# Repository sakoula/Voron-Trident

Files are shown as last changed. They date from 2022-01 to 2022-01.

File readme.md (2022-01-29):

# Voron Trident

<!-- MarkdownTOC -->

- [Very Important Links](#very-important-links)
- [Crimping Microfits](#crimping-microfits)
- [Voron Afterburner PCB setup](#voron-afterburner-pcb-setup)
- [Fysetc Spider Wiring](#fysetc-spider-wiring)
- [Klipper Firmware](#klipper-firmware)
    - [Current Config](#current-config)
    - [Other Configs](#other-configs)
    - [Motor Configuration](#motor-configuration)
    - [Bed Heater Thermistor](#bed-heater-thermistor)
    - [Hotend Thermistor](#hotend-thermistor)
- [Initial Setup](#initial-setup)
    - [Motor Setup](#motor-setup)
    - [Configuring Limits](#configuring-limits)
    - [Inductive Probe](#inductive-probe)
    - [PID Tune](#pid-tune)
    - [Bed Levelling](#bed-levelling)
    - [Z Offset Adjustment](#z-offset-adjustment)
    - [FUN](#fun)
    - [Extruder Calibration \(e-steps\)](#extruder-calibration-e-steps)
    - [Bed Mesh](#bed-mesh)
- [Notes from Steve Build](#notes-from-steve-build)
- [Spider Setup](#spider-setup)
    - [WARNING](#warning)
    - [Flash Bootloader](#flash-bootloader)
    - [Install Klipper](#install-klipper)
    - [Compile Klipper for USB connectivity](#compile-klipper-for-usb-connectivity)
    - [Compile Klipper for GPIO connectivity](#compile-klipper-for-gpio-connectivity)
    - [Flash Firmware](#flash-firmware)
- [Shopping List](#shopping-list)
- [Neopixels](#neopixels)

<!-- /MarkdownTOC -->

# Very Important Links
[up up up](#)

- [Print-Tuning-Guide](https://github.com/AndrewEllis93/Print-Tuning-Guide)
- [Docs](https://docs.vorondesign.com/)
- [Calculating Driver Current Settings](https://docs.vorondesign.com/community/howto/120decibell/calculating_driver_current.html)

some mods

- [Logan's mods](https://github.com/LoganFraser/VoronMods)

# Crimping Microfits
[up up up](#)

- [Crimping Microfits](https://www.youtube.com/watch?v=jM3Xfs3Nie4&t=66s)

correct way to insert crimp to microfit3:

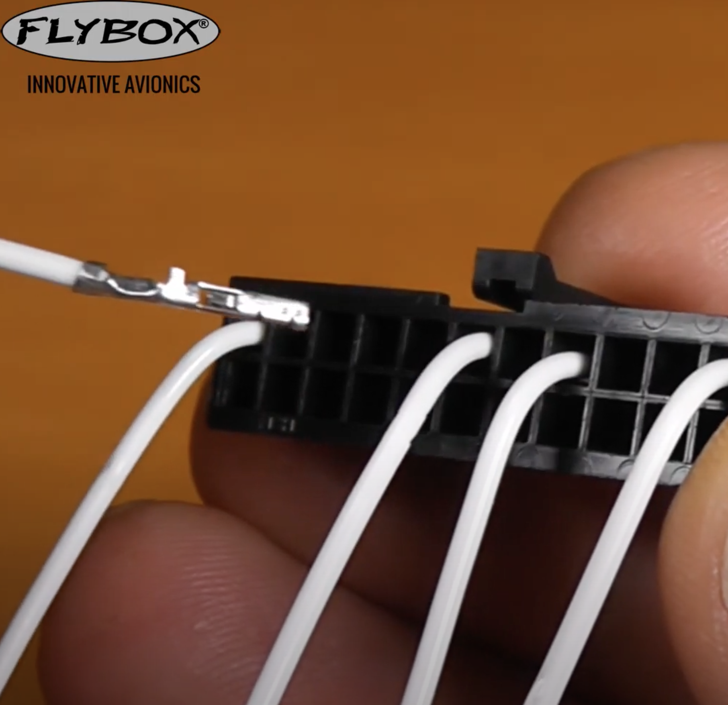
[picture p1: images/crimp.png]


- [Crimps](https://github.com/AndrewEllis93/Print-Tuning-Guide#crimps)

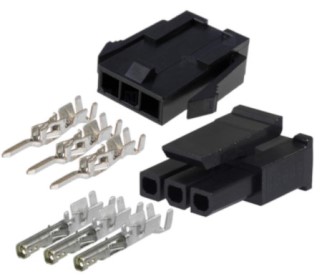
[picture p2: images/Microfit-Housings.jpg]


# Voron Afterburner PCB setup
[up up up](#)

**Pinout**

```
20/Red    24V  - HE0 +V
20/Black  GND  - PSU -V (NOT MAINS GND)
24/Red    PROBE/ABL  - Probe Signal Pin
20/Black  HE0  - Hotend Heater -V
24/Red    CT   - Chamber Thermistor Signal Pin (TH1)
24/Black  PCF  - Part Cooling Fan -V
24/Black  HEF  - Hotend Cooling Fan -V
24/Black  AGND - Hotend Thermistor -V
24/Red    TH0  - Hotend Thermistor Signal Pin (TH0)
24/Red    S1A  - Red Stepper Wire
24/Black  S2A  - Green Stepper Wire
24/Red    S1B  - Blue Stepper Wire
24/Black  S2B  - Black Stepper Wire
no        XES  - X Endstop Signal Pin
```

I did the wiring according to the following:

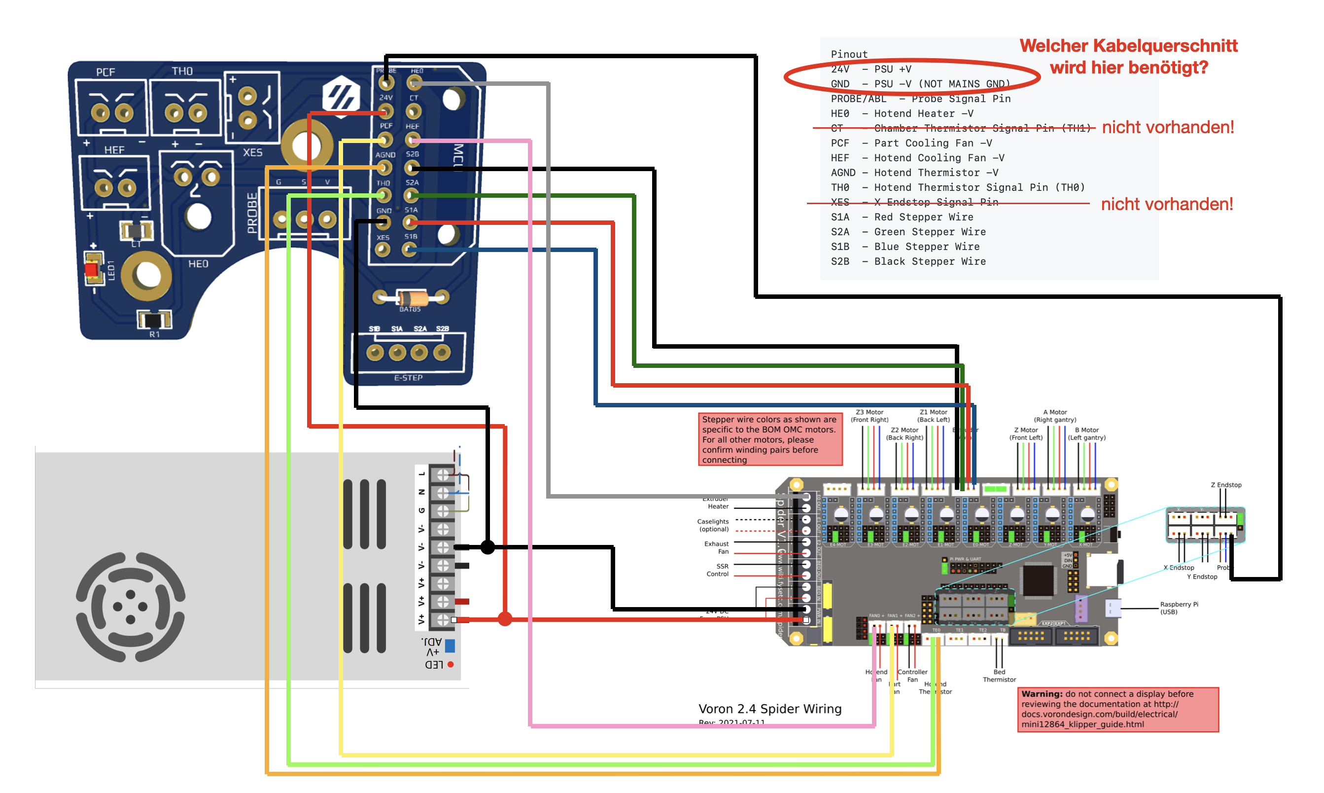
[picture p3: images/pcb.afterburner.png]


# Fysetc Spider Wiring
[up up up](#)

Read the following: [Voron V2 - Fysetc Spider Wiring](https://docs.vorondesign.com/build/electrical/v2_spider_wiring.html#voron-v2---fysetc-spider-wiring)

it referenced here that for the jumpers we need to do (do not put a jumper on the jst port):

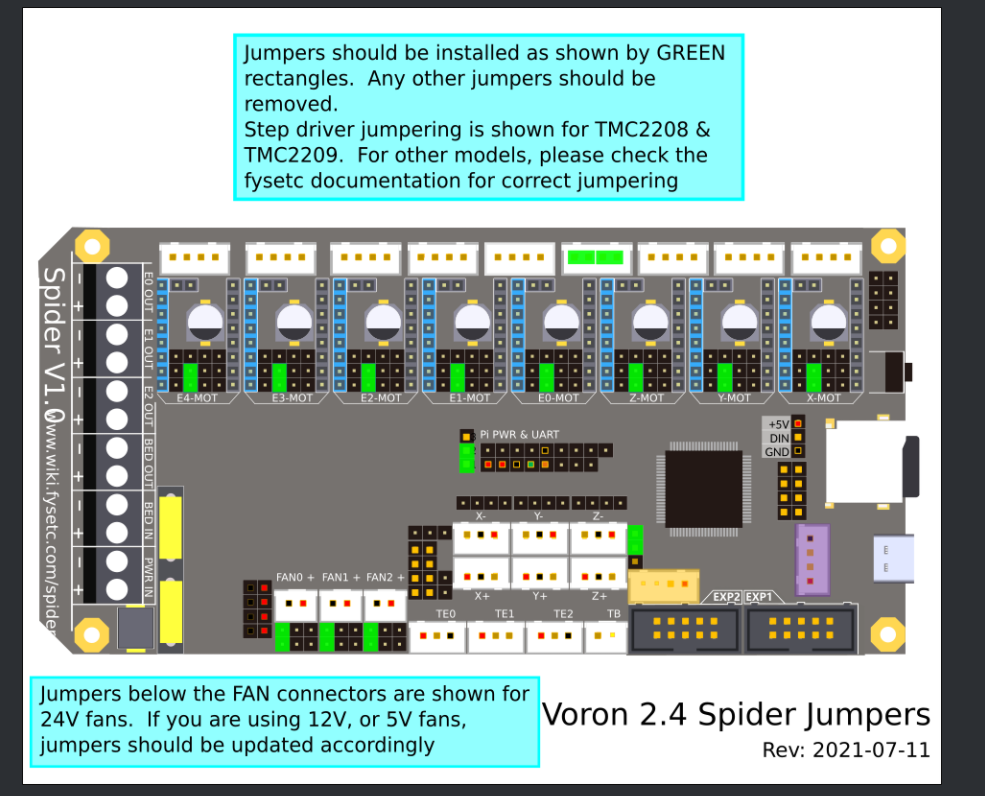
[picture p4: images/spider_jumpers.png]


you can also check [mhoush](https://github.com/VoronDesign/VoronUsers/tree/master/firmware_configurations/klipper/jaeger/Spider_1.1_V1.8) for wiring.

I connected the X/Y end stops as following:

* X endstop to X-
* Y endstop to Y-

Regarding how you cable the motors wires in a discussion with @jaeger (github id mhoush) he mentioned:

> The only reason for that is that's what color order MY stepper motors had Apparently there's no real standard for it. So with that said the colors aren't as important as the windings. If you're not sure or don't have data from the stepper manufacturer, you can identify windings by shorting two of the wires together (with the stepper unplugged) If it gets harder to turn by hand, those two wires are a winding (winding = πηνίο)

check [(LDO-42STH20-1004ASHVRN-RevA-technical-datasheet.pdf]((LDO-42STH20-1004ASHVRN-RevA-technical-datasheet.pdf) which states that fot he exrtruder motor we have the windings pairs are Black/A-Green/C and Red/B-Blue/D These are wired into the After Burner PCB:

| Type | Winding 1  | Winding 1 | Winding 2 | Winding 2 |
| ---- | --- | --- | ---| --- |
| Cable  | Black | Green | Red | Blue |
| PCB | S1B | S1A | S2A | S2B |
| Spider | A2 | A1 | B1 | B2 |

Regarding the motor wiring I did:

* M1 - X-MOT - Z-LEFT
* M2 - Y-MOT  - A
* M3 - Z-MOT  - Empty
* M4 - E0-MOT  - E
* M5 - E1-MOT  - Z-RIGHT
* M6 - E2-MOT  - Z-REAR
* M7 - E3-MOT  - B
* M8 - E4-MOT  - Empty

# Klipper Firmware
[up up up](#)

## Current Config

**My current configuration is this [printer.cfg](printer.cfg)**

## Other Configs

* [sample_firmwares/trident-spider-1.1.majarspeed.cfg](sample_firmwares/trident-spider-1.1.majarspeed.cfg) from [github](https://github.com/VoronDesign/Voron-Trident/pull/31/files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)
* [sample_firmwares/trident-spider-1.1.mhoush.cfg](sample_firmwares/trident-spider-1.1.mhoush.cfg) from [github](https://github.com/mhoush/Voron-Trident/blob/main/Firmware/Voron_Trident_Spider_1.1.cfg)
* [sample_firmwares/trident-spider-1.1.nkalogerinis.cfg](sample_firmwares/trident-spider-1.1.nkalogerinis.cfg) from nick

start [here](https://docs.vorondesign.com/build/software/configuration.html)

## Motor Configuration

we currently have:

* X/Y: LDO-42STH40-2004MAC(VRN) [datasheet of hi temp equivalent](HT_LDO-42STH40-2004MAH_VRN_RevA-technical-datasheet.pdf) 0.9° Step Angle/400 Steps/2 Amp/350mN-m Holding Torque/130C 
* Ex1: LDO-42STH20-1004ASH-MM(VRN) [datasheet](LDO-42STH20-1004ASHVRN-RevA-technical-datasheet.pdf) 1.8° Step Angle/200 Steps/1.0A/18Ncm Holding Torque/180C
* Zx3: LDO-42STH40-1684L300E(VRN) [datasheet](LDO-42STH40-1684L300EVRN-RevA-technical-datasheet.pdf) 1.8° Step Angle/200 Steps/1.68A/450Nm Holding Torque/130C

calculate currents based on [Calculating Driver Current Settings ](https://docs.vorondesign.com/community/howto/120decibell/calculating_driver_current.html). And avoid specifying hold current because klipeer says [so](https://www.klipper3d.org/TMC_Drivers.html#prefer-to-not-specify-a-hold_current)

* X/Y: `run_current = 2 * 0.707 = 1.414`, `hold_current = run_current * 0.6 = 0.8484`
* Zx3: `run_current = 1.68 * 0.707 = 1.1877`, `hold_current = run_current * 0.6 = 0.712`
* Ex1: `run_current = 1 * 0.707 = 0.7`, `hold_current = run_current * 0.6 = 0.42`

Go with conservative configs, microsteps 32 and interpolation off. Do not setup hold_current. Mainly use the settings in octopus config. run currents are calculated based on 70% of the run_rurrent

```yaml
[stepper_x]
microsteps: 32
full_steps_per_rotation: 400  # 200 for 1.8 degree motors, 400 for 0.9 degree

[tmc2209 stepper_x]
uart_pin: PA15
interpolate: False
run_current: 1.0
sense_resistor: 0.110
stealthchop_threshold: 0

[stepper_y]
microsteps: 32
full_steps_per_rotation: 400  # 200 for 1.8 degree motors, 400 for 0.9 degree

[tmc2209 stepper_y]
uart_pin: PE15
interpolate: False
run_current: 1.0
sense_resistor: 0.110
stealthchop_threshold: 0
```

```yaml
[stepper_z1]
microsteps: 32

[tmc2209 stepper_z1]
uart_pin: PC15
interpolate: False
run_current: 0.7
sense_resistor: 0.110
stealthchop_threshold: 0
```

```yaml
[extruder]
microsteps: 32

[tmc2209 extruder]
uart_pin: PD7
interpolate: False
run_current: 0.5
sense_resistor: 0.110
stealthchop_threshold: 0
```

## Bed Heater Thermistor

Thermistor used in the Keenovo is a 'NTC 100K thermistor (Beta 25/50 3950K-1%)' based on the [fermio site](https://fermio.xyz/keenovo-international-group-limited/keenovo-silicone-heatmat-290-x-290mm-230-v-ac-400-w/)

from [klipper config](https://www.klipper3d.org/Config_Reference.html#extruder)

```
sensor_type:
#   Type of sensor - common thermistors are "EPCOS 100K B57560G104F",
#   "ATC Semitec 104GT-2", "ATC Semitec 104NT-4-R025H42G", "Generic
#   3950","Honeywell 100K 135-104LAG-J01", "NTC 100K MGB18-104F39050L32",
#   "SliceEngineering 450", and "TDK NTCG104LH104JT1". See the
#   "Temperature sensors" section for other sensors. This parameter
#   must be provided.
```

```yaml
sensor_type: Generic 3950
```

## Hotend Thermistor

got [(vonwange) ATC Semitec 104GT-2](https://vonwange.com/product/vonwange-atc-semitec-104gt-2/)

```yaml
[extruder]
sensor_type: ATC Semitec 104GT-2
```

# Initial Setup
[up up up](#)

* [Initial Startup Checks ](https://docs.vorondesign.com/build/startup/)
* [Configuration checks¶](https://www.klipper3d.org/Config_checks.html)

## Motor Setup

```console
STEPPER_BUZZ STEPPER=stepper_x
STEPPER_BUZZ STEPPER=stepper_y
STEPPER_BUZZ STEPPER=stepper_z
STEPPER_BUZZ STEPPER=stepper_z1
STEPPER_BUZZ STEPPER=stepper_z2
STEPPER_BUZZ STEPPER=extruder

QUERY_ENDSTOPS
```

check this try to do a home x and y and invert pins if required

```yaml
dir_pin: PD6
```

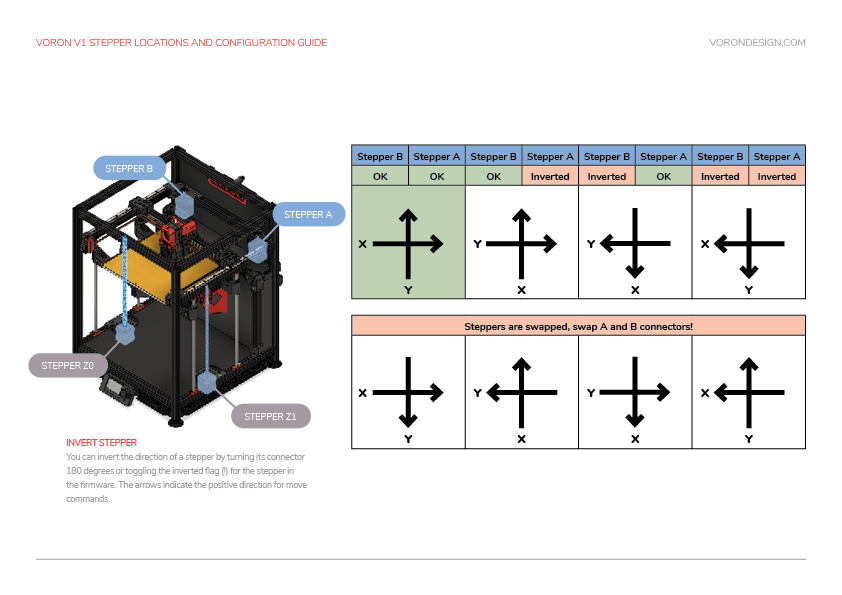
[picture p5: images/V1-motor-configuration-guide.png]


## Configuring Limits

```gcode
G90
G28 X Y
G1 X300.00 Y300.00 F7800
G1 X0.00 Y0.00 F7800
M114 # get current location
G1 X300.00 Y0.00 F7800
G1 X0.00 Y300.00 F7800
G90
G1 X170.00 Y300.00 F7800
```

Figure out where Z-Endstop is update [homing_override] or [safe_z_home] with those values. For me it is 170

## Inductive Probe

```
G28 X Y Z
QUERY_PROBE
# move bed close to nozzle
QUERY_PROBE
// probe: TRIGGERED
// PROBE_ACCURACY at X:150.000 Y:149.000 Z:35.000 (samples=10 retract=3.000 speed=5.0 lift_speed=5.0)
08:21:06  // probe at 150.000,149.000 is z=8.280000
08:21:08  // probe at 150.000,149.000 is z=8.281250
08:21:10  // probe at 150.000,149.000 is z=8.281250
08:21:11  // probe at 150.000,149.000 is z=8.281250
08:21:13  // probe at 150.000,149.000 is z=8.281250
08:21:15  // probe at 150.000,149.000 is z=8.281250
08:21:16  // probe at 150.000,149.000 is z=8.281250
08:21:18  // probe at 150.000,149.000 is z=8.281250
08:21:19  // probe at 150.000,149.000 is z=8.281250
08:21:21  // probe at 150.000,149.000 is z=8.281250
08:21:21  // probe accuracy results: maximum 8.281250, minimum 8.280000, range 0.001250, average 8.281125, median 8.281250, standard deviation 0.000375
```

## PID Tune

```
G28 X Y Z
G90
G1 Z7.00 F7800
PID_CALIBRATE HEATER=heater_bed TARGET=60
// PID parameters: pid_Kp=40.922 pid_Ki=1.057 pid_Kd=395.922

M106 S100
PID_CALIBRATE HEATER=extruder TARGET=210
// PID parameters: pid_Kp=25.246 pid_Ki=1.476 pid_Kd=107.925
```

## Bed Levelling

verify that the following are under the probe:

```yaml
points:
    30, 5
    150, 245
    270, 5
```

For this process **NEVER** have the part fan on

```
G28 X Y
G90
G1 X30.00 Y5.00 F7800
G1 X150.00 Y245.00 F7800
G1 X270.00 Y5.00 F7800

SET_HEATER_TEMPERATURE HEATER=extruder TARGET=210
SET_HEATER_TEMPERATURE HEATER=heater_bed TARGET=60

G28 X Y Z
G90
G1 Z10.00 F7800
# allow some time needed for the probe to stabilize ~ 5 min
# wait until standard deviation < 0.003
PROBE_ACCURACY
G1 Z10.00 F7800
Z_TILT_ADJUST
```

## Z Offset Adjustment

```
G28
BED_MESH_CLEAR
Z_ENDSTOP_CALIBRATE
TESTZ Z=-30.0
TESTZ Z=-2.0
TESTZ Z=-0.3
ACCEPT
```

The Z offset can be adjusted during a print using the Tune menu on the display, and the printer configuration can be updated with this new value. Remember that higher values for the position_endstop means that the nozzle will be closer to the bed.

**Important:** Klipper assumes that this process is being done cold. If being performed hot, do an additional TESTZ Z=-0.1 before accepting.

## FUN

```
M117 Homing...
G28 Y0 X0 Z0
Z_TILT_ADJUST
BED_MESH_CALIBRATE
```

## Extruder Calibration (e-steps)

```
SET_HEATER_TEMPERATURE HEATER=extruder TARGET=210
# measure 120mm and tie a tie wrap
extrude twice 50mm and measure
measured 21mm
New Config Value = Old Config Value * (Actual Extruded Amount/Target Extruded Amount)
22.4899598 = 22.6789511 * (119/120)
```

## Bed Mesh

I tried a bed mesh with cold bed and got the following results:

```
#*# [bed_mesh default]
#*# version = 1
#*# points =
#*#       0.002500, 0.011250, 0.006250, 0.016250, 0.005000
#*#       0.007500, 0.003750, -0.001250, 0.007500, -0.011250
#*#       0.027500, 0.013750, 0.000000, 0.003750, -0.015000
#*#       0.046250, 0.018750, -0.000000, 0.002500, -0.015000
#*#       0.070000, 0.025000, 0.002500, 0.005000, -0.018750
#*# tension = 0.2
#*# min_x = 40.0
#*# algo = bicubic
#*# y_count = 5
#*# mesh_y_pps = 2
#*# min_y = 40.0
#*# x_count = 5
#*# max_y = 260.0
#*# mesh_x_pps = 2
#*# max_x = 260.0
```

I posted on discord and it is good:

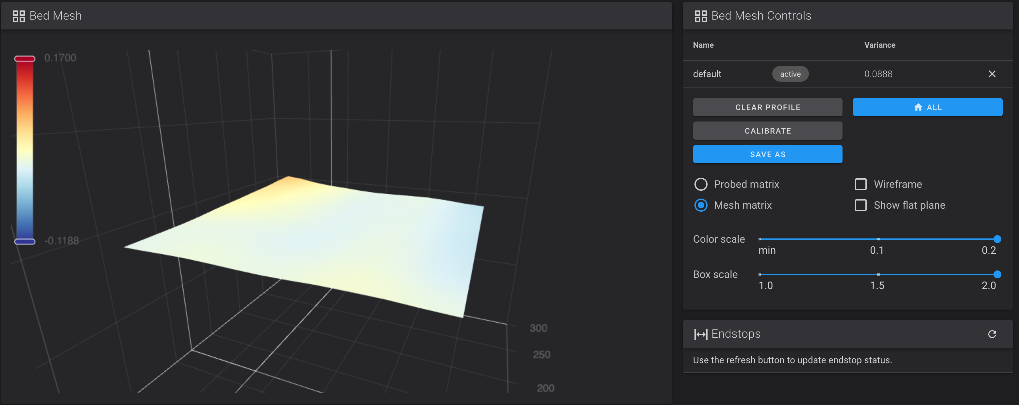
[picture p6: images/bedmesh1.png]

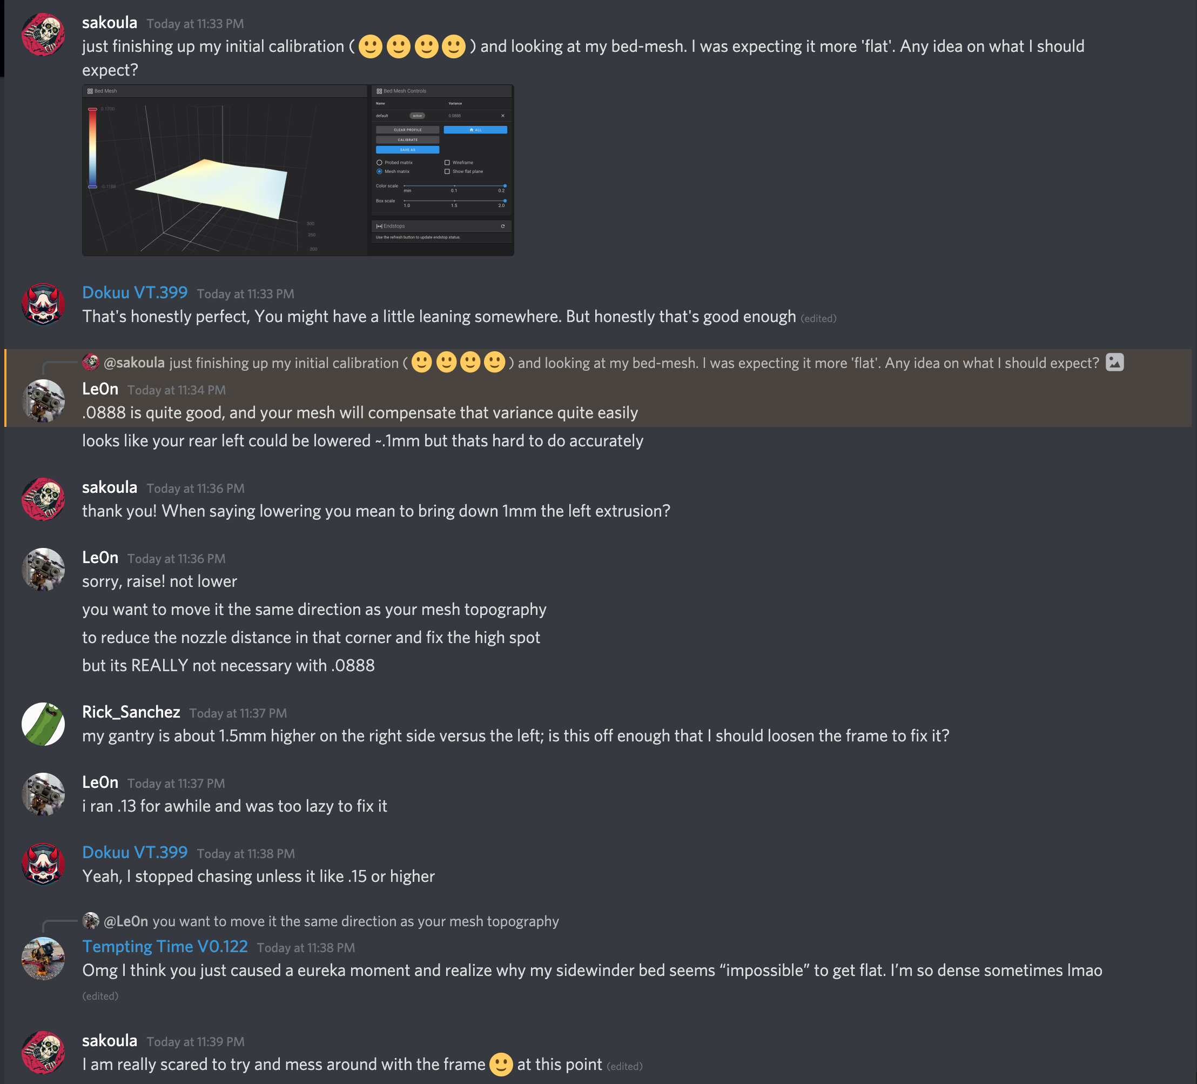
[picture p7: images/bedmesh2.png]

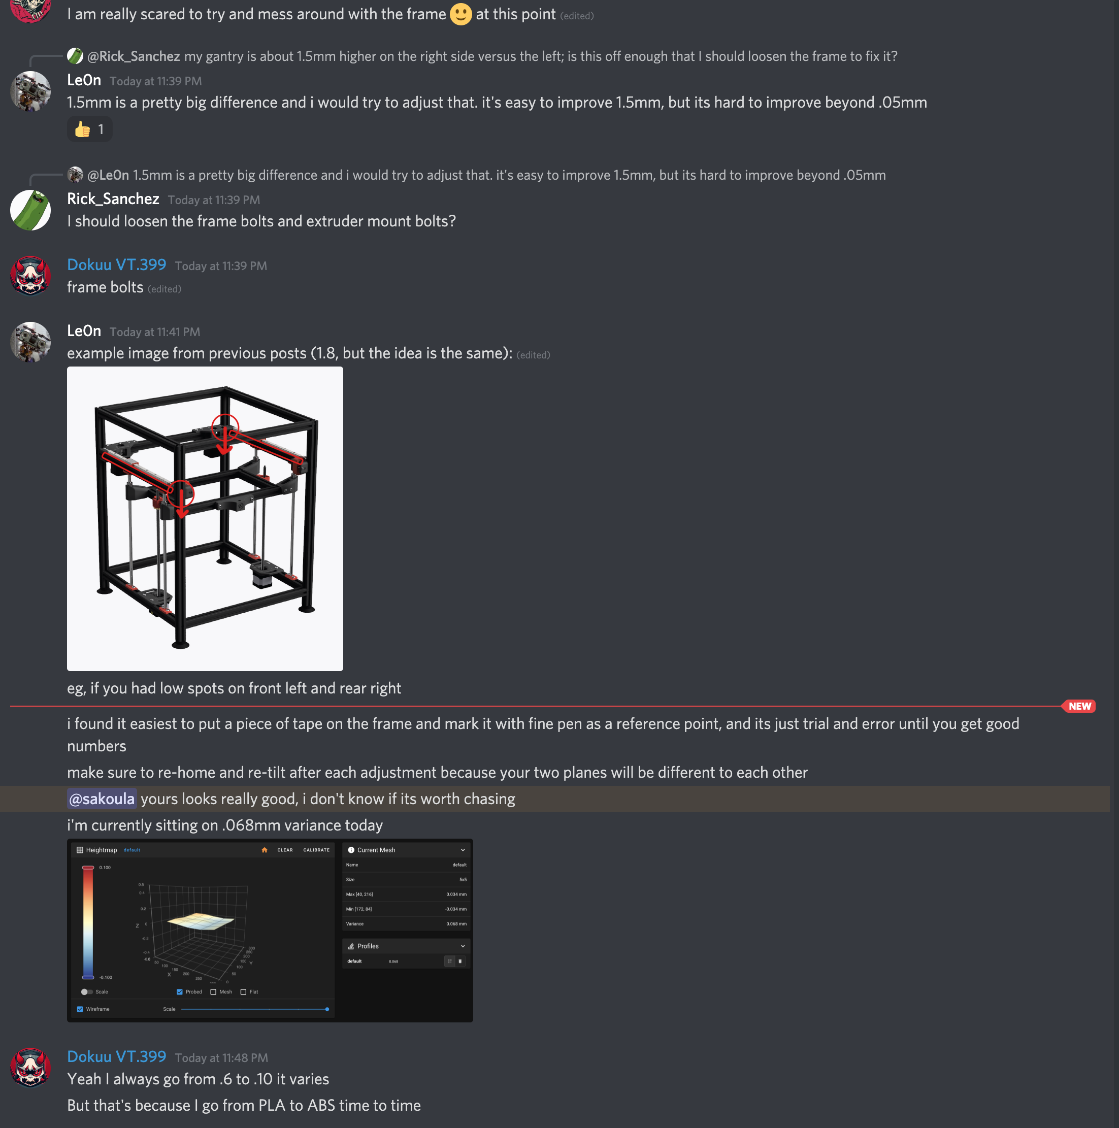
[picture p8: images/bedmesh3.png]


# Notes from Steve Build

* nozzle to probe is about 2-3mm. I got it to 4mm
* igus chains 18 links
* washer ground/bed
* x igus chain fixed end on the toolhead to be as horizontal as possible
* y igus chain fixed end on front on the accent piece to be as horizontal as possible
* end stop octapus for probe
* probe uses 24V
* 2209 use UART
* connected pi to spider over pins
    * power use 20AWG
    * tx/rx use 24AWG

# Spider Setup
[up up up](#)

## WARNING
[up up up](#)

Before putting the drivers follow [this procedure](https://github.com/FYSETC/FYSETC-SPIDER/blob/main/Spider%203.3v%20issue.md) and according to [this](https://discord.com/channels/460117602945990666/822468097637875712/896816322279768084)

1. Power off the motherboard completely (remove the wiring completely), and wait for the 24v, 5v and 3.3v LEDs to be completely off.
2. Connect a 100K resistor (or a cable) to the +/- pole of MAIN_PWR. **Wait 10 minutes and disconnect it**
3. Connect a 100K resistor (or a cable) to the +/- pole of VMOT. **Wait 10 minutes and disconnect it**
4. Wait for 5-10 minutes, plug in the driver, and perform firmware and other operations.

## Flash Bootloader
[up up up](#)

This is the [procedure](https://github.com/FYSETC/FYSETC-SPIDER/tree/main/bootloader). You really do not need to do this part. According to FYSETC every board that leaves the factory [has already a bootloader on](https://github.com/FYSETC/FYSETC-SPIDER#441-upload-the-firmwaresdcard). However since there have been two versions of bootloaders lets put the latest 32k one.

Power off board, remove SD Card, and

- place jumper on BT0 and 3.3V. (Between Z- endstop and E0 driver). **This is on the right of the PI PWR & UART in the middle of the board. Place one jumper horizontally**
- Connect Spider to Pi with USB cable with jumper in place. 
- Set U5V jumper closest to stepper driver modules to power Spider from the Pi USB (you can power it with 24V I preferred this way). **The U5V jumper left of the PI PWR & UART in the middle of the board**

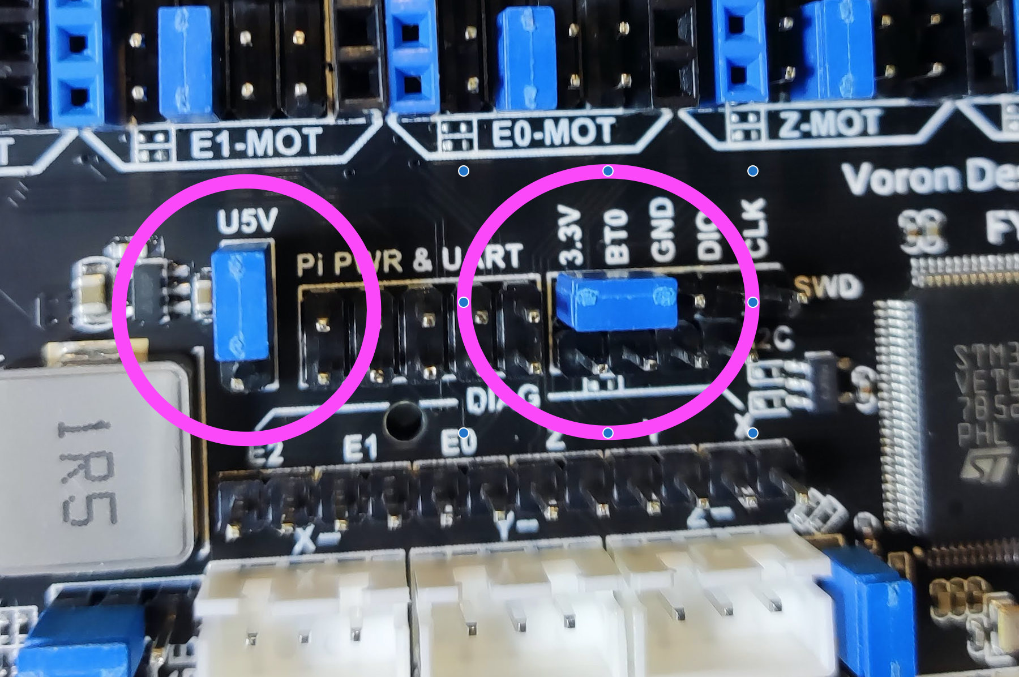
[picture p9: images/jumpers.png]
jumpers


on the pi type:

```console
$ apt-get install dfu-util
$ dfu-util --list

dfu-util 0.9

Copyright 2005-2009 Weston Schmidt, Harald Welte and OpenMoko Inc.
Copyright 2010-2016 Tormod Volden and Stefan Schmidt
This program is Free Software and has ABSOLUTELY NO WARRANTY
Please report bugs to http://sourceforge.net/p/dfu-util/tickets/

Found DFU: [0483:df11] ver=2200, devnum=3, cfg=1, intf=0, path="1-1.2", alt=3, name="@Device Feature/0xFFFF0000/01*004 e", serial="STM32FxSTM32"
Found DFU: [0483:df11] ver=2200, devnum=3, cfg=1, intf=0, path="1-1.2", alt=2, name="@OTP Memory /0x1FFF7800/01*512 e,01*016 e", serial="STM32FxSTM32"
Found DFU: [0483:df11] ver=2200, devnum=3, cfg=1, intf=0, path="1-1.2", alt=1, name="@Option Bytes  /0x1FFFC000/01*016 e", serial="STM32FxSTM32"
Found DFU: [0483:df11] ver=2200, devnum=3, cfg=1, intf=0, path="1-1.2", alt=0, name="@Internal Flash  /0x08000000/04*016Kg,01*064Kg,03*128Kg", serial="STM32FxSTM32"

$ wget https://github.com/FYSETC/FYSETC-SPIDER/raw/main/bootloader/Bootloader_FYSETC_SPIDER.hex

$ objcopy --input-target=ihex --output-target=binary Bootloader_FYSETC_SPIDER.hex Bootloader_FYSETC_SPIDER.bin && dfu-util -a 0 -s 0x08000000:mass-erase:force -D Bootloader_FYSETC_SPIDER.bin

Copyright 2005-2009 Weston Schmidt, Harald Welte and OpenMoko Inc.
Copyright 2010-2016 Tormod Volden and Stefan Schmidt
This program is Free Software and has ABSOLUTELY NO WARRANTY
Please report bugs to http://sourceforge.net/p/dfu-util/tickets/

dfu-util: Invalid DFU suffix signature
dfu-util: A valid DFU suffix will be required in a future dfu-util release!!!
Opening DFU capable USB device...
ID 0483:df11
Run-time device DFU version 011a
Claiming USB DFU Interface...
Setting Alternate Setting #0 ...
Determining device status: state = dfuERROR, status = 10
dfuERROR, clearing status
Determining device status: state = dfuIDLE, status = 0
dfuIDLE, continuing
DFU mode device DFU version 011a
Device returned transfer size 2048
DfuSe interface name: "Internal Flash  "
Performing mass erase, this can take a moment
Setting timeout to 35 seconds
Downloading to address = 0x08000000, size = 20260
Download	[=========================] 100%        20260 bytes
Download done.
File downloaded successfully
```

keep U5V on powering by USB (closest to stepper driver modules) do not power from 24V yet.

## Install Klipper
[up up up](#)

use [kiauh](https://github.com/th33xitus/kiauh)

install everything as pi
```bash
pi@thor ~$ cd /home/pi/kiauh
./kiauh.sh

install klipper
install moonraker 1 instance
install fluidd (install MJPG-Streamer)
```

## Compile Klipper for USB connectivity
[up up up](#)

```console
$ cd klipper
$ make menuconfig

enable extra low-level configuration options
Micro-controller Architecture `STMicroelectronics STM32`
Processor model `STM32F446`
Clock reference `12 MHz crystal`
Boot address 32k
Communication interface USB (on PA11/PA12)

make
```

copy `out/klipper.bin` to an sdcard as FAT32 and place it on the root directory with the name `firmware.bin`.

## Compile Klipper for GPIO connectivity
[up up up](#)

```console
$ cd klipper
$ make menuconfig

enable extra low-level configuration options
Micro-controller Architecture `STMicroelectronics STM32`
Processor model `STM32F446`
Bootloader offset (32KiB bootloader)
Clock reference `12 MHz crystal`
Communication interface (Serial (on USART1 PA10/PA9))

make
```

copy `out/klipper.bin` to an sdcard as FAT32 and place it on the root directory with the name `firmware.bin`.

```console
pi@thor ~$ sudo raspi-config
3 Interface Options    Configure connections to peripherals
P6 Serial Port Enable/disable shell messages on the serial connection
Would you like a login shell to be accessible over serial? <No>
Would you like the serial port hardware to be enabled? <Yes>

add at /boot/config.txt
dtoverlay=pi3-disable-bt

remove from /boot/cmdline.txt any instance of "console=serial0,115200" or "console=ttyAMA0,115200"
```

## Flash Firmware
[up up up](#)

make sure that you have shutdown everything. place the SDCARD on spider and connect pi via usb. Power on pi and let everything boot.

goto pi and type:

```console
$ ls -l /dev/serial/by-id/
total 0
lrwxrwxrwx 1 root root 13 Oct 10 17:45 usb-Klipper_stm32f446xx_1D0032000250563046353420-if00 -> ../../ttyACM0
```

edit the klipper printer.cfg and enter the following (from klipper config [repository](https://github.com/Klipper3d/klipper/blob/master/config/generic-fysetc-spider.cfg) ):

```yaml
# This file contains common pin mappings for the Fysetc Spider board.
# To use this config, the firmware should be compiled for the STM32F446.
# When calling "menuconfig", enable "extra low-level configuration setup"
# and select the "12MHz crystal" as clock reference.
# For flashing, write the compiled klipper.bin to memory location 0x08000000

# See docs/Config_Reference.md for a description of parameters.

[stepper_x]
step_pin: PE11
dir_pin: PE10
enable_pin: !PE9
microsteps: 16
rotation_distance: 40
endstop_pin: PB14  # PA1 for X-max
position_endstop: 0
position_max: 200

[stepper_y]
step_pin: PD8
dir_pin: PB12
enable_pin: !PD9
microsteps: 16
rotation_distance: 40
endstop_pin: ^PB13  # PA2 for Y-max
position_endstop: 0
position_max: 200

[stepper_z]
step_pin: PD14
dir_pin: PD13
enable_pin: !PD15
microsteps: 16
rotation_distance: 8
endstop_pin: PA0  # PA3 for Z-max
position_endstop: 0
position_max: 400

[extruder]
step_pin: PD5
dir_pin: !PD6
enable_pin: !PD4
microsteps: 16
rotation_distance: 33.500
nozzle_diameter: 0.400
filament_diameter: 1.750
heater_pin: PB15
sensor_type: EPCOS 100K B57560G104F
sensor_pin: PC0
control: pid
pid_Kp: 22
pid_Ki: 1.08
pid_Kd: 114
min_temp: 0
max_temp: 260

#[extruder1]
#step_pin: PE6
#dir_pin: !PC13
#enable_pin: !PE5
#heater_pin: PC8
#sensor_pin: PC1

#[extruder2]
#step_pin: PE2
#dir_pin: !PE4
#enable_pin: !PE3
#heater_pin: PB3
#sensor_pin: PC2

#[extruder3]
#step_pin: PD12
#dir_pin: PC4
#enable_pin: !PE8

#[extruder4]
#step_pin: PE1
#dir_pin: !PE0
#enable_pin: !PC5

[heater_bed]
heater_pin: PB4
sensor_type: EPCOS 100K B57560G104F
sensor_pin: PC3
control: watermark
min_temp: 0
max_temp: 130

#fan for printed model FAN0
[fan]
pin: PB0

#fan for hotend FAN1
#[heater_fan my_nozzle_fan]
#pin: PB1
#shutdown_speed: 1

#fan for control board FAN2
#[heater_fan my_control_fan]
#pin: PB2

#####################################################################
# LED Control
#####################################################################

#[output_pin caselight ]
##  Chamber Lighting - In 5V-RGB Position
#pin: PD3
#pwm: true
#shutdown_value: 0
#value:100
#cycle_time: 0.01

[mcu]
## Obtain definition by "ls -l /dev/serial/by-id/" then unplug to verify
serial: /dev/serial/by-id/usb-Klipper_Klipper_firmware_12345-if00

[printer]
kinematics: cartesian
max_velocity: 300
max_accel: 3000
max_z_velocity: 5
max_z_accel: 100

########################################
# TMC UART configuration
########################################

#[tmc2208 stepper_x]
#uart_pin: PE7
#run_current: 0.8
#hold_current: 0.5
#stealthchop_threshold: 999999

#[tmc2208 stepper_y]
#uart_pin: PE15
#run_current: 0.8
#hold_current: 0.5
#stealthchop_threshold: 999999

#[tmc2208 stepper_z]
#uart_pin: PD10
#run_current: 0.8
#hold_current: 0.5
#stealthchop_threshold: 999999

#[tmc2208 extruder]
#uart_pin: PD7
#run_current: 0.8
#hold_current: 0.5
#sense_resistor: 0.110
#stealthchop_threshold: 999999

#[tmc2208 extruder1]
#uart_pin: PC14
#run_current: 0.8
#hold_current: 0.5
#stealthchop_threshold: 999999

#[tmc2208 extruder2]
#uart_pin: PC15
#run_current: 0.8
#hold_current: 0.5
#stealthchop_threshold: 999999

#[tmc2208 extruder3]
#uart_pin: PA15
#run_current: 0.8
#hold_current: 0.5
#stealthchop_threshold: 999999

#[tmc2208 extruder4]
#uart_pin: PD11
#run_current: 0.8
#hold_current: 0.5
#stealthchop_threshold: 999999

########################################
# TMC SPI configuration
########################################

#[tmc2130 stepper_x]
#spi_bus: spi4
#cs_pin: PE7
#diag1_pin: PB14
#run_current: 0.800
#hold_current: 0.500
#stealthchop_threshold: 999999

#[tmc2130 stepper_y]
#spi_bus: spi4
#cs_pin: PE15
#diag1_pin: PB13
#run_current: 0.800
#hold_current: 0.500
#stealthchop_threshold: 999999

#[tmc2130 stepper_z]
#spi_bus: spi4
#cs_pin: PD10
#diag1_pin: PA0
#run_current: 0.800
#hold_current: 0.500
#stealthchop_threshold: 999999

#[tmc2130 extruder]
#spi_bus: spi4
#cs_pin: PD7
#diag1_pin: PA3
#run_current: 0.800
#hold_current: 0.500
#stealthchop_threshold: 999999

#[tmc2130 extruder1]
#spi_bus: spi4
#cs_pin: PC14
#diag1_pin: PA2
#run_current: 0.800
#hold_current: 0.500
#stealthchop_threshold: 999999

#[tmc2130 extruder2]
#spi_bus: spi4
#cs_pin: PC15
#diag1_pin: PA1
#run_current: 0.800
#hold_current: 0.500
#stealthchop_threshold: 999999

#[tmc2130 extruder3]
#spi_bus: spi4
#cs_pin: PA15
#run_current: 0.800
#hold_current: 0.500
#stealthchop_threshold: 999999

#[tmc2130 extruder4]
#spi_bus: spi4
#cs_pin: PD11
#run_current: 0.800
#hold_current: 0.500
#stealthchop_threshold: 999999

########################################
# EXP1 / EXP2 (display) pins
########################################

[board_pins]
aliases:
    # EXP2 header
    EXP1_10=<5V>, EXP1_9=<GND>,
    EXP1_8=PD1,   EXP1_7=PD0,
    EXP1_6=PC12,  EXP1_5=PC10,     # Slot in the socket on the other side
    EXP1_4=PD2,   EXP1_3=PC11,
    EXP1_2=PA8,   EXP1_1=PC9,

    # EXP1 header
    EXP2_10=<5V>, EXP2_9=<GND>,
    EXP2_8=<RST>, EXP2_7=PB10,
    EXP2_6=PA7,   EXP2_5=PC7,       # Slot in the socket on the other side
    EXP2_4=PA4,   EXP2_3=PC6,
    EXP2_2=PA5,   EXP2_1=PA6

# See the sample-lcd.cfg file for definitions of common LCD displays.
```

make sure you edit `[mcu]` part
type as root: `systemctl restart klipper`
go to the logs and verify that spider is detected:

```text
mcu 'mcu': Starting serial connect
Loaded MCU 'mcu' 91 commands (v0.10.0-39-g5f184e3f / gcc: (15:7-2018-q2-6) 7.3.1 20180622 (release) [ARM/embedded-7-branch revision 261907] binutils: (2.31.1-11+rpi1+11) 2.31.1)
MCU 'mcu' config: BUS_PINS_i2c1=PB6,PB7 BUS_PINS_i2c2=PB10,PB11 BUS_PINS_spi3a=PC11,PC12,PC10 BUS_PINS_spi2a=PC2,PC3,PB10 BUS_PINS_i2c1a=PB8,PB9 RESERVE_PINS_USB=PA11,PA12 CLOCK_FREQ=180000000 BUS_PINS_spi1a=PB4,PB5,PB3 STATS_SUMSQ_BASE=256 STEP_DELAY=2 ADC_MAX=4095 BUS_PINS_spi4=PE13,PE14,PE12 RESERVE_PINS_crystal=PH0,PH1 BUS_PINS_spi2=PB14,PB15,PB13 BUS_PINS_spi1=PA6,PA7,PA5 BUS_PINS_spi3=PB4,PB5,PB3 MCU=stm32f446xx
Sending MCU 'mcu' printer configuration...
Configured MCU 'mcu' (1024 moves)
Starting heater checks for heater_bed
Starting heater checks for extruder
...
```

shutdown everything, remove sdcard and verify that the `firmware.bin` is not there anymore.

when you  want to upgrade the firmware you will always do it with the sdcard.

# Shopping List
[up up up](#)

- [3M 4910 VHB Tape 6mm x 3M](https://www.aliexpress.com/item/1005002289433427.html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)
- [3M VHB 5608 Double Sided Acrylic Foam Adhesive Tape Waterproof Heavy Duty Mounting Tape Indoor Outdoor Use Free Shipping 5mm x 3m](https://www.aliexpress.com/item/1005002015627817.html)

# Neopixels
[up up up](#)

[yes!](https://discord.com/channels/460117602945990666/822468097637875712/932038192750792754)

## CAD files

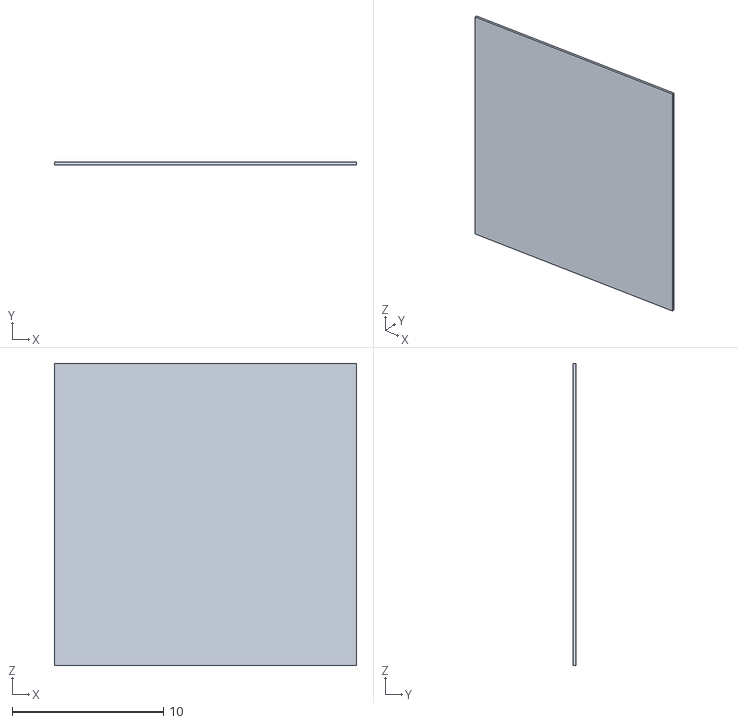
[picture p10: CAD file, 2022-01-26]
calibration_stls/first_layer_calibration.stl
20.0 x 0.2 x 20.0

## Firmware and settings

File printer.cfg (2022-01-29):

[include kiauh_macros.cfg]
## Voron Design Trident FYSETC Spider 1.1 Configuration

## *** THINGS TO CHANGE/CHECK: ***
## MCU paths                          [mcu] section
## Thermistor types                   [extruder] and [heater_bed] sections - See 'sensor types' list at end of file
## Z Endstop Switch location          [homing_override] section
## Z Endstop Switch  offset for Z0    [stepper_z] section
## Probe points                       [quad_gantry_level] section
## Min & Max gantry corner postions   [quad_gantry_level] section
## PID tune                           [extruder] and [heater_bed] sections
## Fine tune E steps                  [extruder] section

##========================== Pin Definitions ========================
## Source: https://github.com/FYSETC/FYSETC-SPIDER


[mcu]
## Uncomment below if you're using the Raspberry uart0 to communicate with Spider
restart_method: command

##  You need to select 'Communication interface' to USB in 'make menuconfig'
##  when you compile Klipper for Spider
##  Obtain definition by "ls -l /dev/serial/by-id/" then unplug to verify
##--------------------------------------------------------------------
# serial: /dev/serial/by-id/usb-Klipper_stm32f446xx_1D0032000250563046353420-if00
##  If you want to use the Raspberry uart0 to communicate with Spider,
##  you need to select 'Communication interface' to 'Serial (on USART1 PA10/PA9)'
##  in 'make menuconfig' when you compile klipper and set the serial as below
##--------------------------------------------------------------------
serial: /dev/ttyAMA0
##--------------------------------------------------------------------

# XXX these values are from Octopus config for Trident repository
[printer]
kinematics: corexy
max_velocity: 300
max_accel: 3000             #Max 4000
max_z_velocity: 15          #Max 15 for 12V TMC Drivers, can increase for 24V
max_z_accel: 50 # XXX what is the right value for this?
square_corner_velocity: 5.0

#####################################################################
#   X/Y Stepper Settings
#####################################################################

## B Drive/Motor M7 / E3-MOT
# E3-MOTOR(7) E3-Step PD12
#             E3-DIR  PC4
#             E3-EN   PE8
#             E3-CS/PDN   PA15
# End-stops   X-MIN   PB14
[stepper_x]
step_pin: PD12
dir_pin: !PC4
enable_pin: !PE8
microsteps: 16
rotation_distance: 40
full_steps_per_rotation: 400  # 200 for 1.8 degree motors, 400 for 0.9 degree
endstop_pin: ^PB14 # X-MIN
position_min: 0

## Uncomment for 250mm build
#position_endstop: 250
#position_max: 250

## Uncomment for 300mm build
position_endstop: 300
position_max: 300

homing_speed: 25            #Max 100
homing_retract_dist: 5
homing_positive_dir: true

# XXX need to revisit these values
[tmc2209 stepper_x]
uart_pin: PA15
interpolate: True
run_current: 0.8
sense_resistor: 0.110
stealthchop_threshold: 0

## A Drive/Motor M2 / EY-MOT
# Y-MOTOR(2) Y-Step  PD8
#            Y-DIR   PB12
#            Y-EN    PD9
#            Y-CS/PDN    PE15
# End-stops  Y-MIN PB13
[stepper_y]
step_pin: PD8
dir_pin: !PB12
enable_pin: !PD9
microsteps: 16
rotation_distance: 40
full_steps_per_rotation: 400  # 200 for 1.8 degree motors, 400 for 0.9 degree
endstop_pin: ^PB13 # Y-MIN

## Uncomment for 250mm build
#position_endstop: 250
#position_max: 250

## Uncomment for 300mm build
position_endstop: 300
position_max: 300

homing_speed: 25            #Max 100
homing_retract_dist: 5
homing_positive_dir: true

# XXX need to revisit these values
[tmc2209 stepper_y]
uart_pin: PE15
interpolate: True
run_current: 0.8
sense_resistor: 0.110
stealthchop_threshold: 0

#####################################################################
#   Z Stepper Settings
#####################################################################

## Z-LEFT Drive/Motor M1/X-MOT
# X-MOTOR(1)  X-Step  PE11
#             X-DIR   PE10
#             X-EN    PE9
#             X-CS/PDN    PE7
# End-stops   Z-MIN PA0
[stepper_z]
step_pin: PE11
dir_pin: PE10
enable_pin: !PE9
microsteps: 16
rotation_distance: 4 # Rotation Distance for TR8x8 = 8, TR8x4 = 4, TR8x2 = 2
full_steps_per_rotation: 200  # 200 for 1.8 degree motors, 400 for 0.9 degree
endstop_pin: ^PA0 # Z-MIN
##  Z-position of nozzle (in mm) to z-endstop trigger point relative to print surface (Z0)
##  (+) value = endstop above Z0, (-) value = endstop below
##  Increasing position_endstop brings nozzle closer to the bed
##  After you run Z_ENDSTOP_CALIBRATE, position_endstop will be stored at the very end of your config
# Remember that higher values for the position_endstop means that the nozzle will be closer to the bed.
#position_endstop: -0.5
# position_endstop: 0.840
position_endstop: 0.920

## All builds use same Max Z
# position_max: 250
# XXX I changed max to 230
position_max: 230
position_min: -2.5
homing_speed: 8.0 # Leadscrews are slower than 2.4, 10 is a recommended max.
second_homing_speed: 3.0
homing_retract_dist: 3.0

# XXX need to revisit these values
[tmc2209 stepper_z]
uart_pin: PE7
interpolate: True
run_current: 0.7
sense_resistor: 0.110
stealthchop_threshold: 0

## Z-REAR Drive/Motor M6/E2-MOT
# E2-MOTOR(6) E2-Step PE2
#             E2-DIR  PE4
#             E2-EN   PE3
#             E2-CS/PDN   PC15
[stepper_z1]
step_pin: PE2
dir_pin: PE4
enable_pin: !PE3
microsteps: 16
rotation_distance: 4          # TR8x8: 8, TR8x4: 4, TR8x2: 2
full_steps_per_rotation: 200  # 200 for 1.8 degree motors, 400 for 0.9 degree

# XXX need to revisit these values
[tmc2209 stepper_z1]
uart_pin: PC15
interpolate: True
run_current: 0.7
sense_resistor: 0.110
stealthchop_threshold: 0

## Z-RIGHT Drive/Motor M5/E1-MOT
# E1-MOTOR(5) E1-Step PE6
#             E1-DIR  PC13
#             E1-EN   PE5
#             E1-CS/PDN   PC14
[stepper_z2]
step_pin: PE6
dir_pin: PC13
enable_pin: !PE5
microsteps: 16
rotation_distance: 4          # TR8x8: 8, TR8x4: 4, TR8x2: 2
full_steps_per_rotation: 200  # 200 for 1.8 degree motors, 400 for 0.9 degree

# XXX need to revisit these values
[tmc2209 stepper_z2]
uart_pin: PC14
interpolate: True
run_current: 0.7
sense_resistor: 0.110
stealthchop_threshold: 0

#####################################################################
#   Extruder Settings
#####################################################################

## E Extruder Motor M4/E0-MOT
# E0-MOTOR(4) E0-Step PD5
#             E0-DIR  PD6
#             E0-EN   PD4
#             E0-CS/PDN   PD7
[extruder]
step_pin: PD5
dir_pin: PD6
enable_pin: !PD4

##  Update value below when you perform extruder calibration
##  If you ask for 100mm of filament, but in reality it is 98mm:
##  rotation_distance = <previous_rotation_distance> * <actual_extrude_distance> / 100
##  22.6789511 is a good starting point
rotation_distance: 22.4899598   #Bondtech 5mm Drive Gears
##  Update Gear Ratio depending on your Extruder Type
##  Use 50:17 for Afterburner/Clockwork (BMG Gear Ratio)
##  Use 80:20 for M4, M3.1
gear_ratio: 50:17               #BMG Gear Ratio
microsteps: 32
full_steps_per_rotation: 200    #200 for 1.8 degree, 400 for 0.9 degree
nozzle_diameter: 0.400
filament_diameter: 1.75

heater_pin: PB15
## Validate the following thermistor type to make sure it is correct:
sensor_type: ATC Semitec 104GT-2
sensor_pin: PC0 # TE0 Position
min_temp: 10
max_temp: 275
max_power: 1.0
min_extrude_temp: 170
control: pid
# PID_CALIBRATE HEATER=extruder TARGET=210
#// PID parameters: pid_Kp=25.246 pid_Ki=1.476 pid_Kd=107.925
pid_kp: 25.246
pid_ki: 1.476
pid_kd: 107.925
##  Try to keep pressure_advance below 1.0
#pressure_advance: 0.05
##  Default is 0.040, leave stock
#pressure_advance_smooth_time: 0.040

# XXX need to revisit these values
[tmc2209 extruder]
uart_pin: PD7
interpolate: False
run_current: 0.5
sense_resistor: 0.110
stealthchop_threshold: 0

#####################################################################
#   Bed Heater
#####################################################################

[heater_bed]
##  SSR Pin - Z board, Servo Pin
heater_pin: PB4 # PB3 is E2_OUT - if set to PB4 (BED_OUT) instead, BED_IN needs to be given power!
sensor_type: Generic 3950
sensor_pin: PC3
##  Adjust Max Power so your heater doesn't warp your bed
##  A good starting point is 0.4 W/cm^2
max_power: 0.6
min_temp: 0
max_temp: 120
control: pid
#PID_CALIBRATE HEATER=heater_bed TARGET=60
#// PID parameters: pid_Kp=40.922 pid_Ki=1.057 pid_Kd=395.922
pid_kp: 40.922
pid_ki: 1.057
pid_kd: 395.922

#####################################################################
#   Probe
#####################################################################

## Probe (Z+ label on board)
[probe]
pin: ^PA3
x_offset: 0
y_offset: 25
z_offset: 0
speed: 5
samples: 3
samples_result: median
sample_retract_dist: 3.0
samples_tolerance: 0.006
samples_tolerance_retries: 3

#####################################################################
#   Fan Control
#####################################################################
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

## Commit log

2022-01-25 updated printer.cfg (about to change motor currents)
    [printer.cfg]
2022-01-26 - updated printer.cfg with correct `rotation_distance: 4` for z steppers - updated printer.cfg PRINT_START macro with parameters to delay heating up nozzle - updated printer.cfg with tmc2209 config (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
    [first_layer_calibration.stl, printer.cfg]
2022-01-26 - printer.cfg: connect to spider over serial - firmware.usb.bin: spider klipper firmware for connecting over usb - firmware.serial.bin: spider klipper firmware for connecting over serial
    [printer.cfg]
2022-01-29 - added leds.cfg from SB repo - add changes on readme
    [leds.cfg, printer.cfg]
